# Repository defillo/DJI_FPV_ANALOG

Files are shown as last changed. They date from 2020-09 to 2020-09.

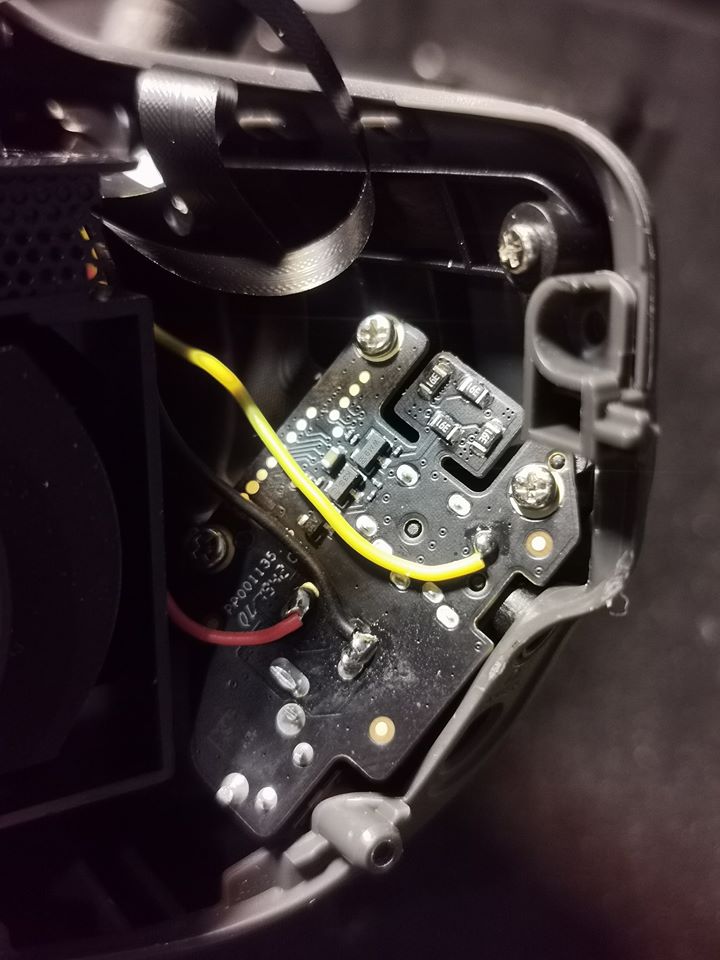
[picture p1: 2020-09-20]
modifica presa interna.jpg

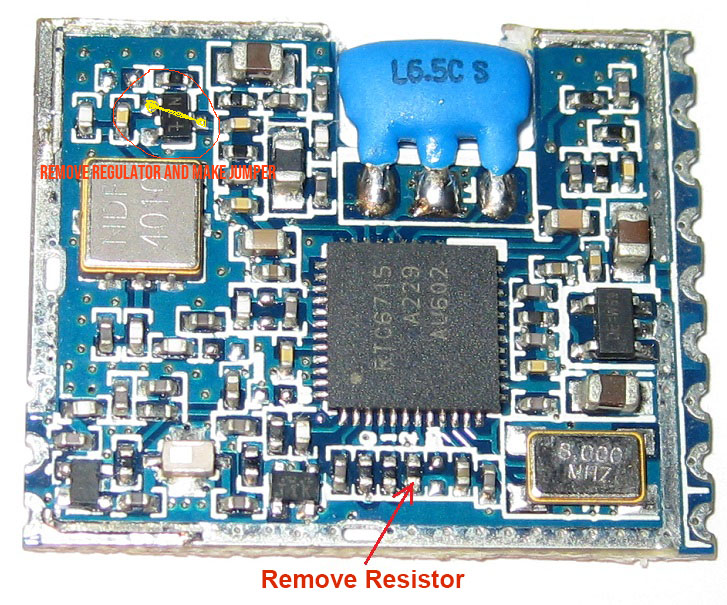
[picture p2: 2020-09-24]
rx5808 mod.png

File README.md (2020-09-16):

# DJI_FPV_ANALOG
Analog diversity receiver, wifi controlled, fitted inside DJI FPV Googles

this project is published for personal use, you can produce and use as many as you want for private use
If you do produce this for commercial purposes, eg. selling this , you're not allowed to do. 
please contact developer if you're interested in this a defilippis1962@gmail.com

DJI ANALOG DIVERSITY MODULES

This boards are made to be fitted inside DJI FPV GOOGLES

Power and video/audio can be taken directly from inside the googles or by cables from outside

Requires two antennas, connected to boards using a uFl connector (one for each board)

Boards control is achieved via wifi connection. Once powered you need to connect to the device in wifi connections,
then start the app and gain control

At present time app runs ONLY in Android. a IOS solution can be provided but it takes time, I will only if the project
will have commercial development

Project use RX5808 modules, opened and modified to work directly at 3V3. 
This means that the internale voltage regulator must be removed and replaced with a small wire from input to output

This modules runs at 3V3 internally, powering at 3V3 reduces power requirements and keeps modules much cooler

Also, you need to check that the data control lines does not have any resistor placed. 
As you need to open the modules to remove the power regulator, you can also check for resistors and in case, remove them

Schematics: description

Main board. 
There is a dc/dc voltage regulator. high efficiency, very low noise, input from 9 up to 36V, 3V3 vout, 1A
All devices on board are 3V3 powered

MCU. it is a Microchip 18F25K22 in QFN footprint. care must be taken in welding

Video Mux: TS5A3154DCUR . this is a dedicate video switch device, to reduce spikes in channel changes. made by Texas Instruments

there are some resistors and caps on board. an inductor also on input part of a low pass filter.

RSSI signal comes from the modules changing from 0.5 (lower rssi) up to 1.2V (higher rssi, saturation)
To enlarge A/D conversion for the MCU (10 bit)  the resistor ladder made by R2-R3-R4 sets proper voltages for 
Vref+  and Vref-  just to have around 1000 steps of resolution for rssi signal
There's a 10 pole ZIF connector for the other board, carrying all the necessary signals

slave board:

there is just the other receiver and the wifi module on this slave board. connected to main board with the ZIF connector

Firmware

Firmware allows to set some parameters and to perform some tasks
Settings:
you can choose to start the modules retriving the last channel or to start with an autoscan to search for higher rssi value

Please keep in mind that to perform a good autosearch, Vtx must be at least 5 meters away, otherwise it will saturate also nearby channels 
resulting in a bad setting. (eg. frequency to be selected 5865, vtx too close it will have a similar signal also for 5870 resulting in a wrong selection)

you can set the hysteresis for switching between one channel to the other. default 10%.
this means that if the difference between the two receiver's rssi values is LESS than 10%, no receiver switch occurs

Low Set: this set the limit below that even a 1% difference in rssi signals causes receiver changes
High set: this set the limit above that no changes occurs for any reasons

Modules must be 'aligned' at first (just one time)

Set the modules in the correct channel with a VTX on, place the VTX 5 meters away and using the app, perform HIGH RSSI setting
Then in the same condition, turn off vtx. be careful not to have other vtx on in the nearings. from APP select the LOW RSSI setting
 to enter this settings, long tap on SETUP in main page, then long tap on SETTINGS on setup page

The wifi name can be changed (apart from the initial DJI_FPV_) in the app. 
There is also a password. this is necessary to stop someone else with the app installed to connect to your googles and play with your channels
dangerous expecially if you're flying ;-)

password default is 0000  . if you forget it, you can boot the device shortening the two pads on the main board, this resets all data to factory default. means you have to redo the max/min rssi procedure

SCAN mode

Scanning is made checking all available channels (analog and DJI digital) providing a 'visual' situation of free frequencies on site
All the channels marked with a red dot are somehow affected by some transmission. this means that rssi on this channels is higher than 5%
When a channel is totally free, rssi is 0%

After scanning you will be able to select a totally free channel very easily

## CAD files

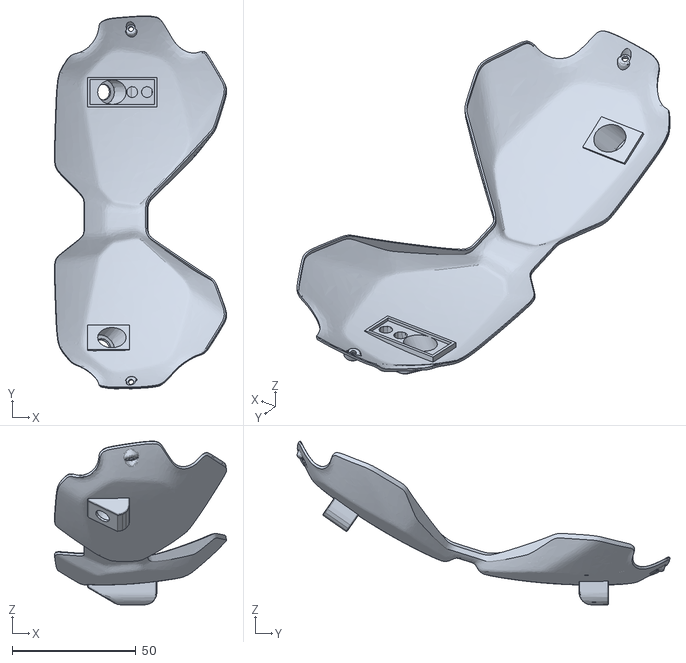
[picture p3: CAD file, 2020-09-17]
DJI FPV googles frontplate external cables.stl
69.7 x 151.0 x 66.3

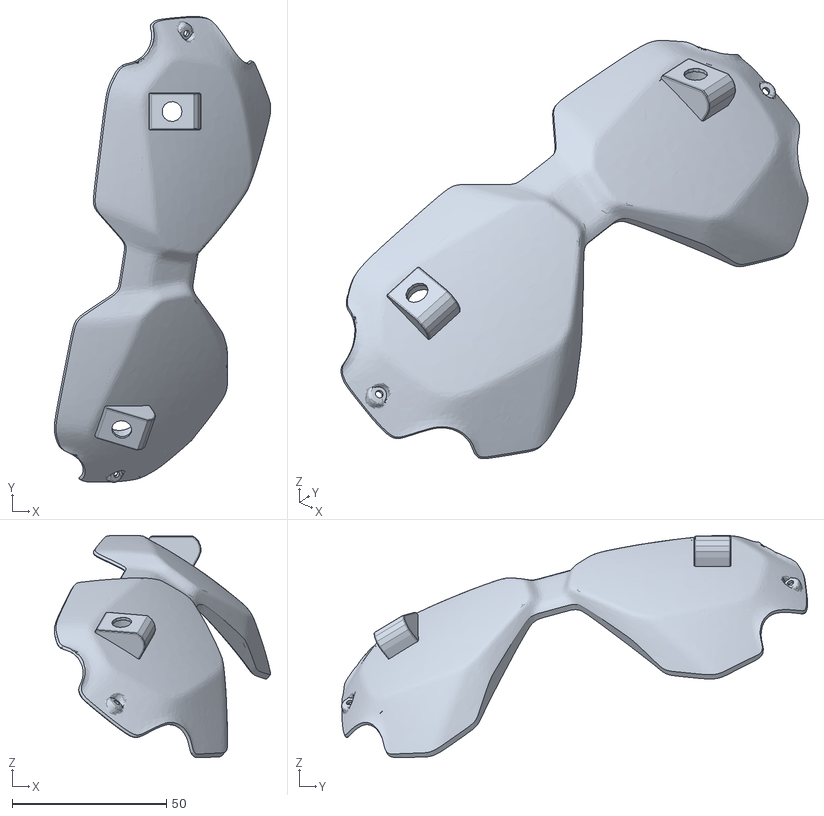
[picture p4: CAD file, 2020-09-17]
DJI FPV googles frontplate internal cables.stl
70.1 x 151.0 x 72.0

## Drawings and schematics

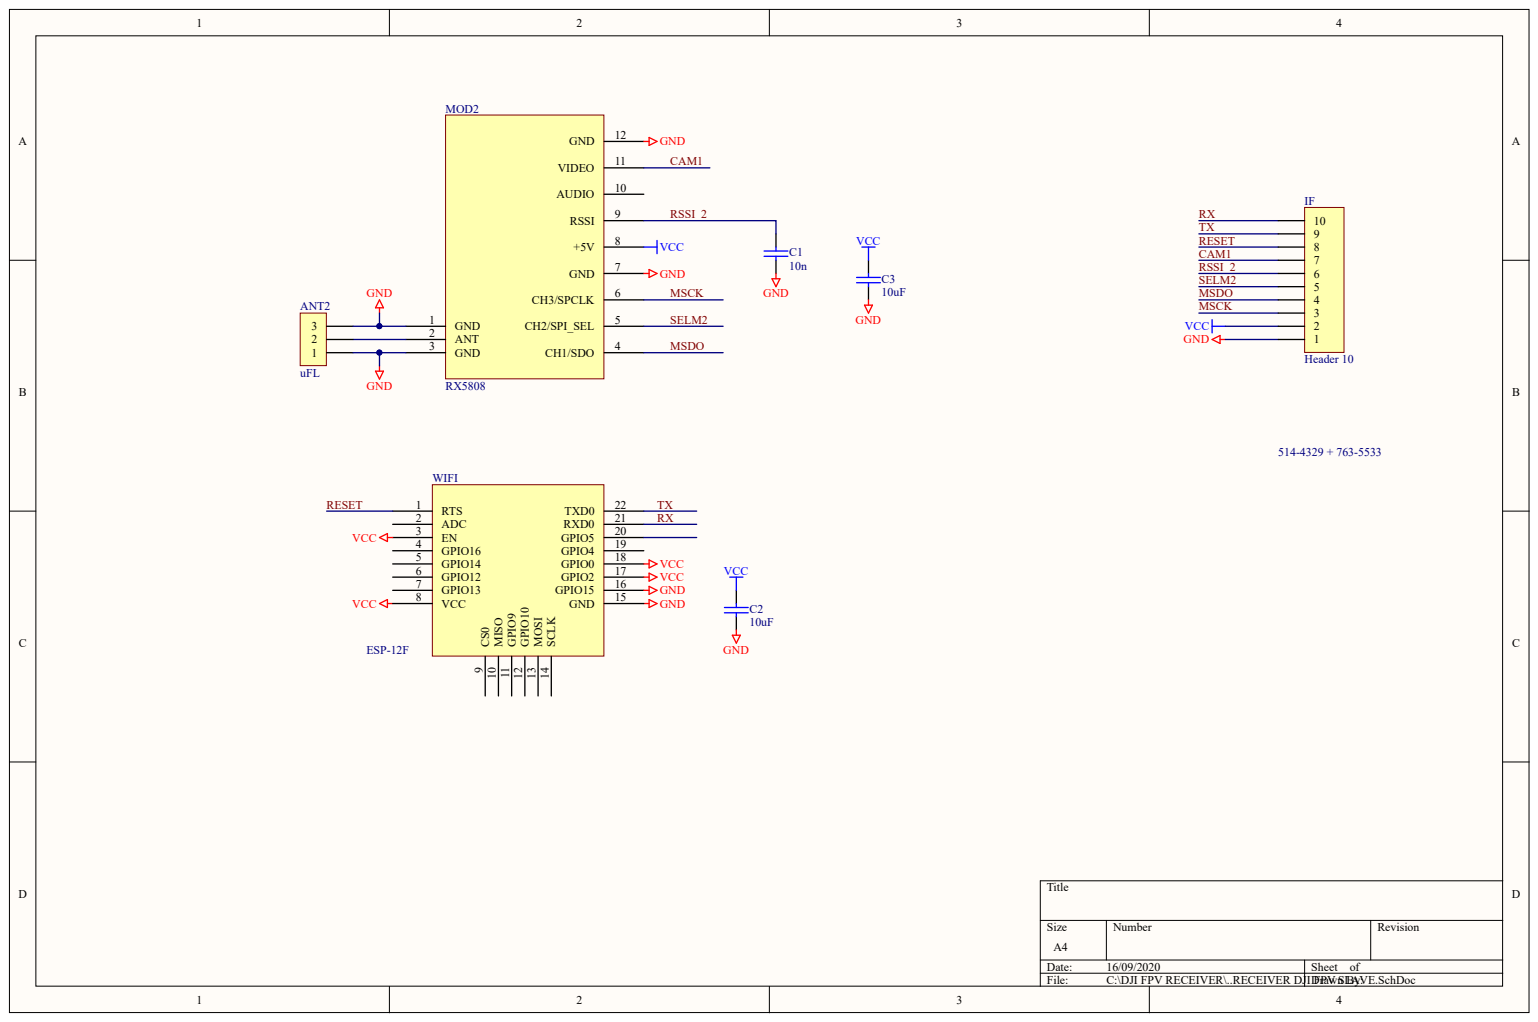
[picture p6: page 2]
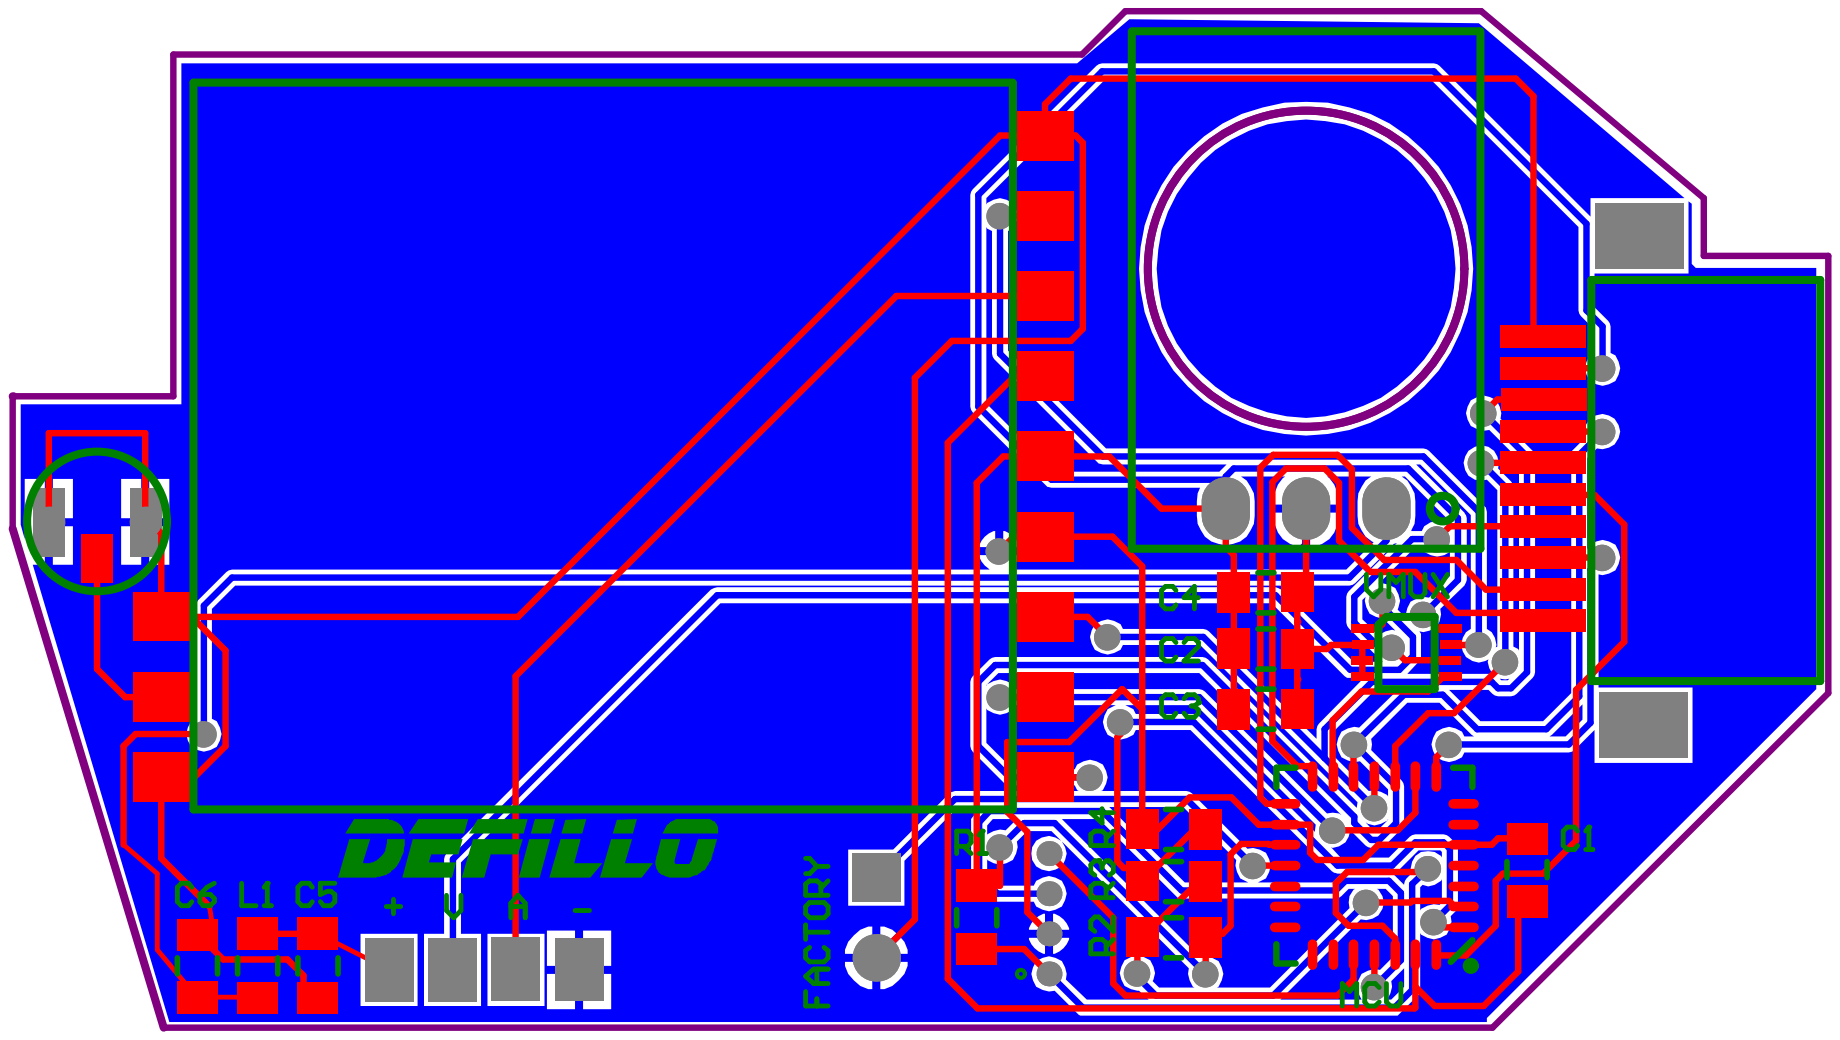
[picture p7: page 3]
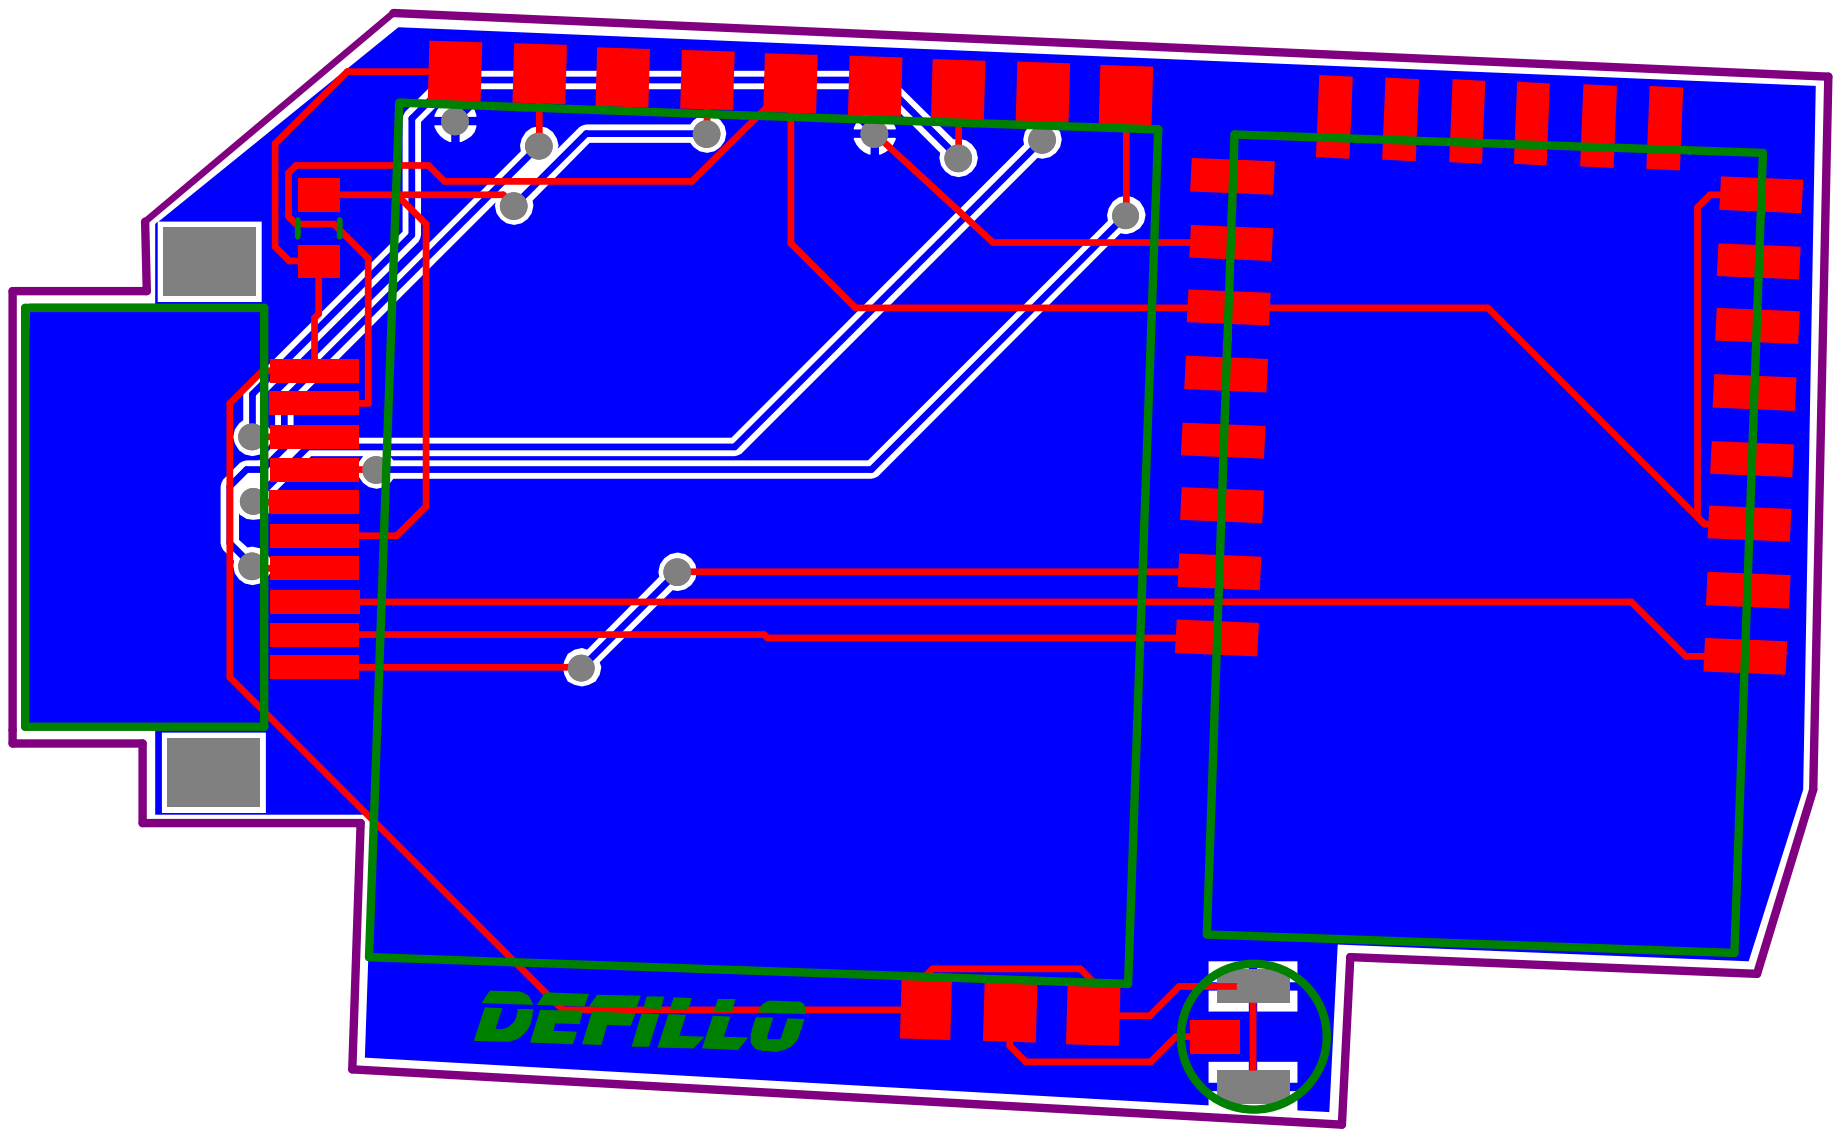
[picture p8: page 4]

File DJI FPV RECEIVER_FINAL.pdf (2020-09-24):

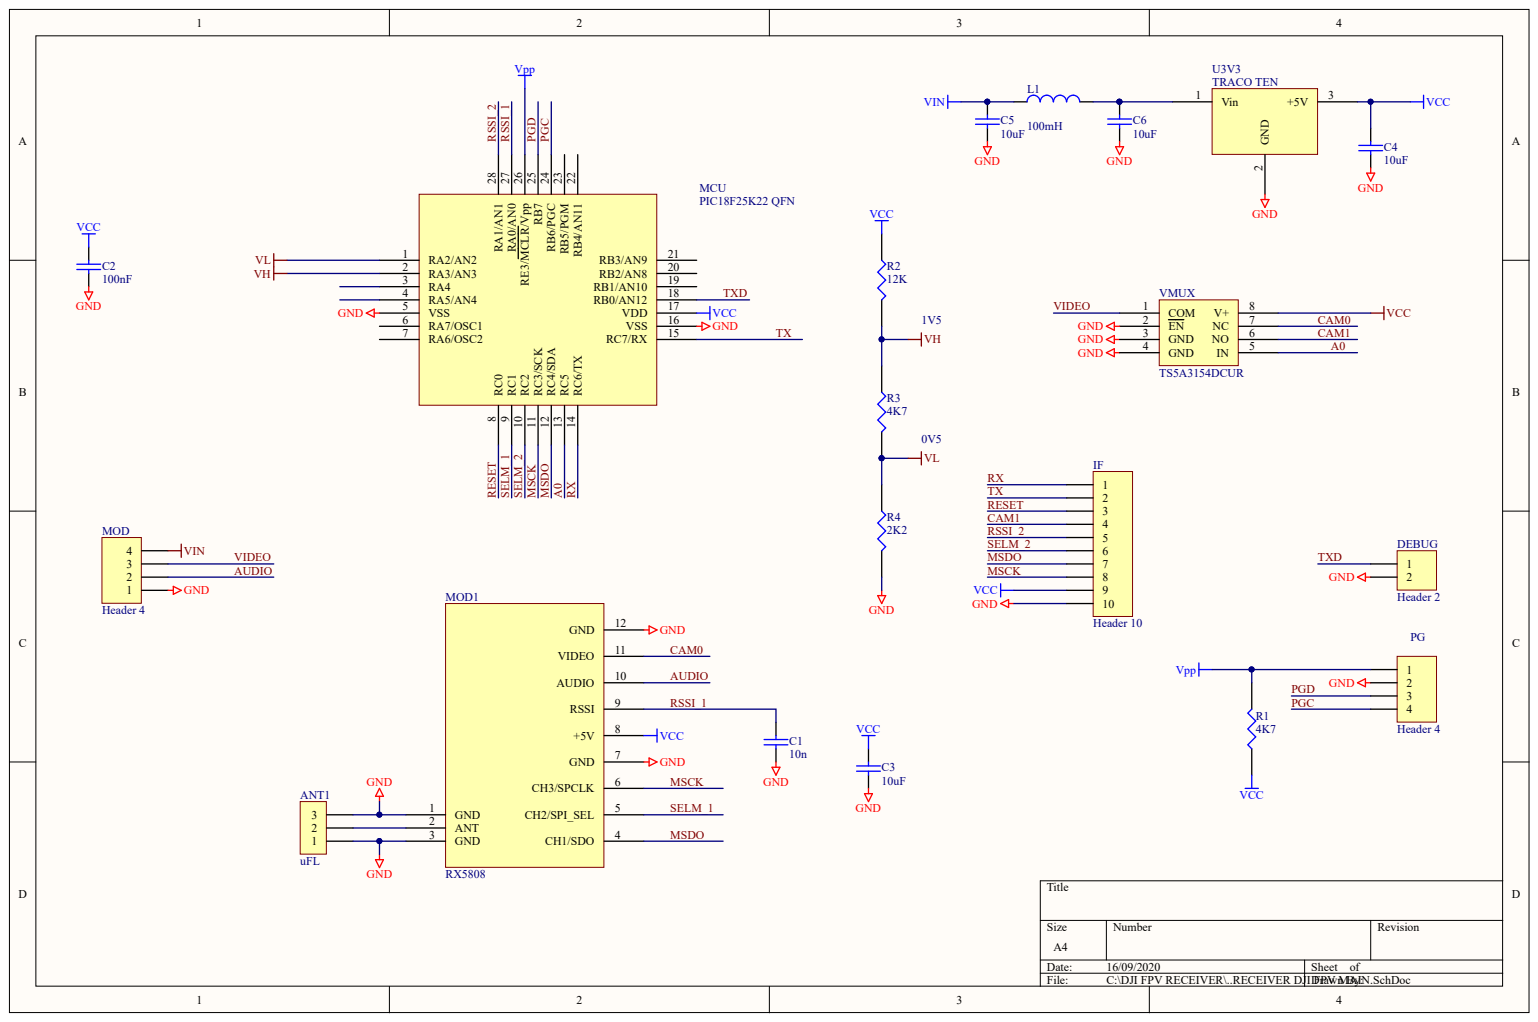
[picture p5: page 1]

B4/AN11 22 RB5/PGM 23 RB6/PGC 24 RB7 25 RE3/MCLR/Vpp 26 RA0/AN0 27 RA1/AN1 28
